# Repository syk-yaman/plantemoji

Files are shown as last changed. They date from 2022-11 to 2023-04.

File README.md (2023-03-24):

# Plantemoji: a smart IoT plant caring system

A smart plant caring and irrigation device with a web infrastructure to monitor and control plants environment and explain their living state in emojis. Basically, your plant will have AI and will be able to talk with you using emojis!

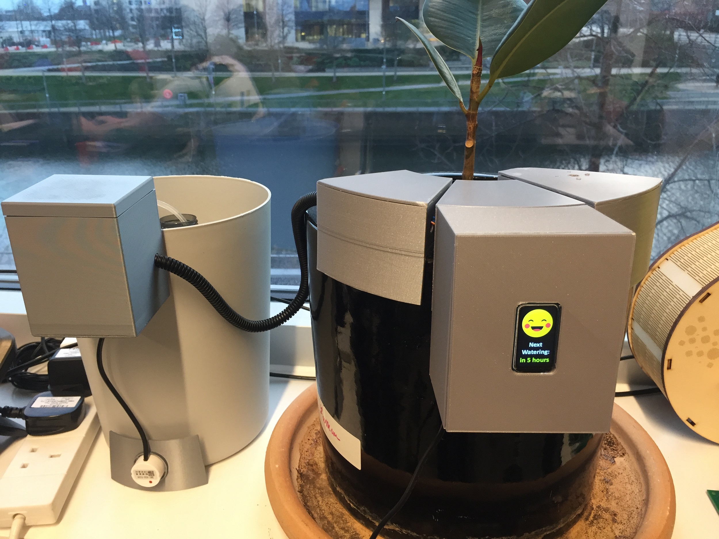
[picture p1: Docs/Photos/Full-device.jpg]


Plant container			          							 |Water bucket	 
:-----------------------------------------------------------:|:-------------------------------------------------------------------------:|
System components overview|   System components overview

## Repository Content Summary

1. **3D Enclosures**

   This section includes the 3D printed parts, namely Fusion360 project files and STLs.

   - [Plant pot](</3D Enclosures/Plant pot/>)
   - [Water bucket](</3D Enclosures/Water bucket/>)

2. **Code**

   Includes micro-controllers' code, Artificial Intelligence code and various assets used during development.

   - [AI](/Code/AI)

     [LSTM.py](/Code/AI/LSTM.py) is the main Python script where the LSTM neural network is developed and trained. This folder also contains the old [Colab experiments](/Code/AI/Colab expirements/), which are obsolete and currently kept for archiving purposes. Finally, the [Results](/Code/AI/Results/) folder, which contains experiments' charts for both the LSTM.py and the obsolete Colab experiments.

   - [Assets](/Code/Assets)

     Contains `.bmp` files to be visualised on the screen, in addition to their original Photoshop files `.psd`

   - [ATMega8A](/Code/ATMega8A)

     C program for the AVR micro-controller.

   - [ESP32](/Code/ESP32)

     C++ code for the main micro-controller, which will replace Huzzah.

   - [Huzzah](/Code/Huzzah)

     C++ code for the old micro-controller. It will replaced by ESP32.

3. **Datasets**

   Includes 1 month dataset (the [full dataset](/Datasets/Full)) and other partial datasets used to train the AI model.

   This section also contains some [data analysis](/Datasets/Analysis/Analysis.md).

4. **Docs**

   This folder holds different kinds of documentation and images produced during project life time.

5. **PCB**

   The electronic side of the project. This section contains Eagle files and CAM outputs sent to PCB manufacturers.

6. **Server**

   Docker Composer file for InfluxDB and Grafana. Basically, all data acquisition is being managed by this Docker image.

## Project Overview

This conceptual diagram explains how the system is composed, down from reading sensors and understanding their values, and later sending them up to the cloud for further analysis and visualisation.

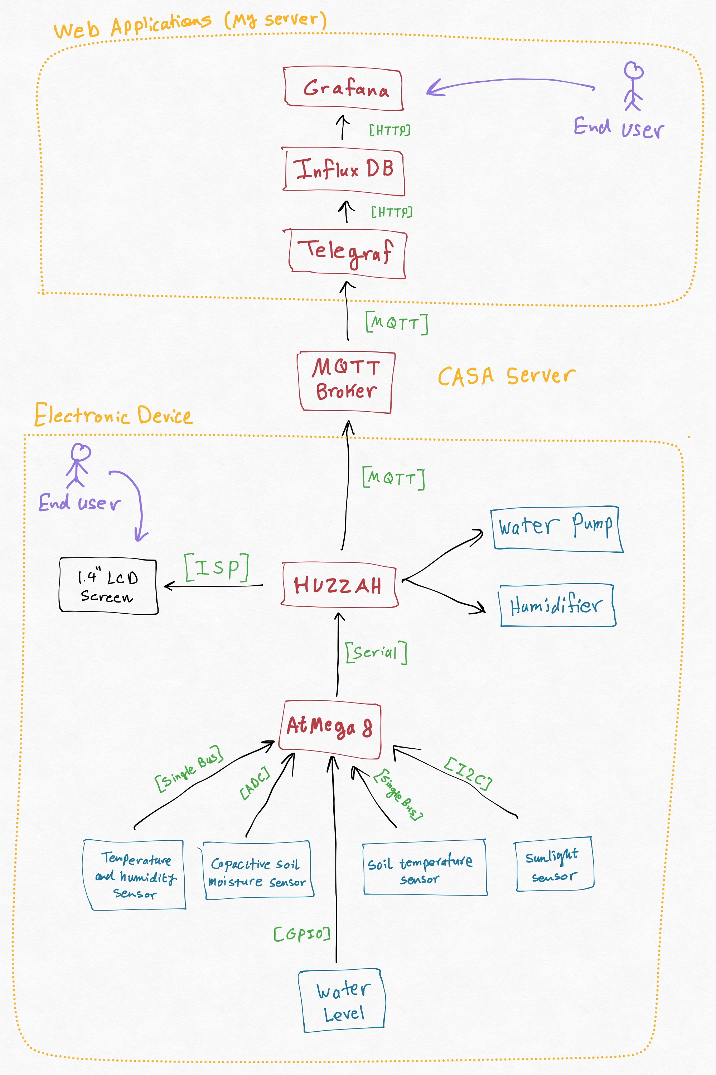
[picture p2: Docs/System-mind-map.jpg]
System components overview


The objectives of this plant monitor are:
 - Interpret sensor data for the end user in a human-friendly way.
 - Take into consideration plant living requirements during the monitoring process.
 - Make comparisons between different soil moisture sensors and the same sensor in different conditions.

## Building

### Used components and tools

Hardware:
 - [Arduino UNO](https://store.arduino.cc/products/arduino-uno-rev3)
 - [Adafruit Feather HUZZAH ESP8266](https://learn.adafruit.com/adafruit-feather-huzzah-esp8266/)
 - Huzzah-DHT22 CASA shield ([From here](https://github.com/ucl-casa-ce/casa0014/blob/main/plantMonitor/README.md#multiple-physical-prototypes))
 - [DH22](https://www.adafruit.com/product/385): Humidity and temperature sensor 
 - [HW-390](https://thepihut.com/products/capacitive-soil-moisture-sensor?variant=32137736421438): Capacitive Soil Moisture Sensor 
 - [Waveshare 1.47" LCD Dislay](https://thepihut.com/products/1-47-rounded-spi-lcd-display-module-172x320?variant=42062646509763)

Software:
 - [InfluxDB](https://www.influxdata.com/)
 - [Telegraf](https://www.influxdata.com/time-series-platform/telegraf/)
 - [Grafana](https://grafana.com/)
 - [Docker Compose](https://docs.docker.com/compose/)

All the software applications are packed into one [Docker image](/Server/docker-compose.yml) that you can use easily.

Tools:
 - [Image2Lcd](https://www.waveshare.com/wiki/File:Image2Lcd.7z): converts BMP images to byte arrays stored in MCUs to be displayed on the LCD screen (please follow [these settings](/Docs/Image2LCD%20app%20settings.jpg)).

### Hardware schematic

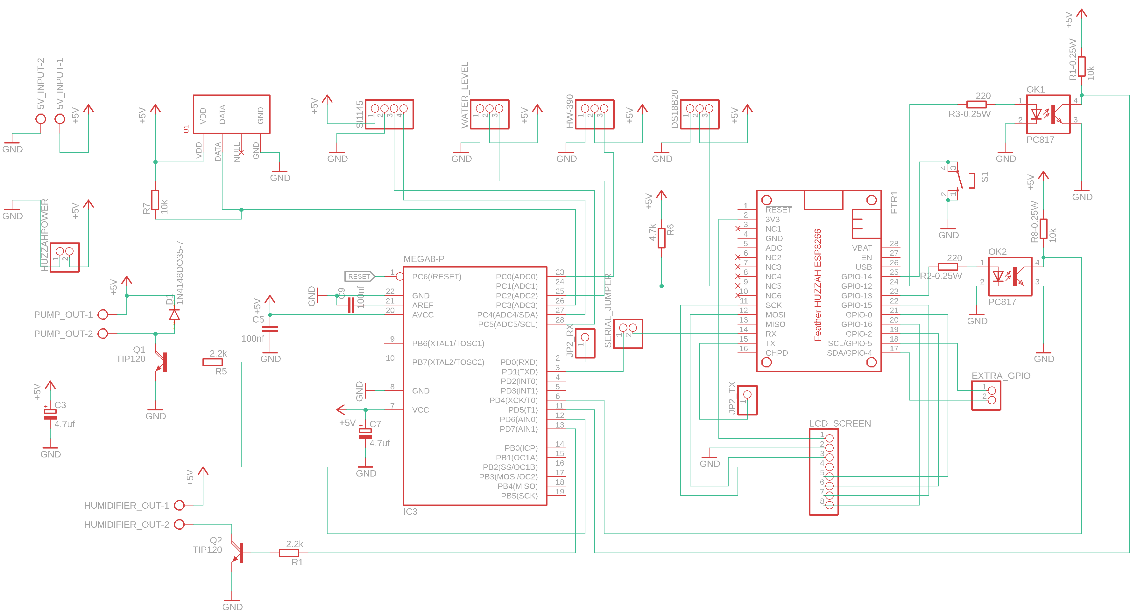
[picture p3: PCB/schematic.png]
Hardware schematic


### Highlights
 - Sensors are connected to Arduino now due to the availability of many ADC ports compared to HUZZAH.
 - The LCD screen driver was ported from Arduino to work on HUZZAH, the latter has more memory and capability to drive screens compared to Arduino.
 - New MQTT topics added: `moistureCapacitive` for the capacitive sensor and `mood` which is derived from sensor data according to plant profile.
 - [Plant profile](/Code/Huzzah/PlantProfile.h): a file containing the suitable living environment parameters for the desired plant. The mood of the plant (happy - sad) is determined based on this profile.

## Results
Grafana dashboard            |  InfluxDB dashboard		 |  MQTT feed
:---------------------------:|:-------------------------:|:-------------------------:
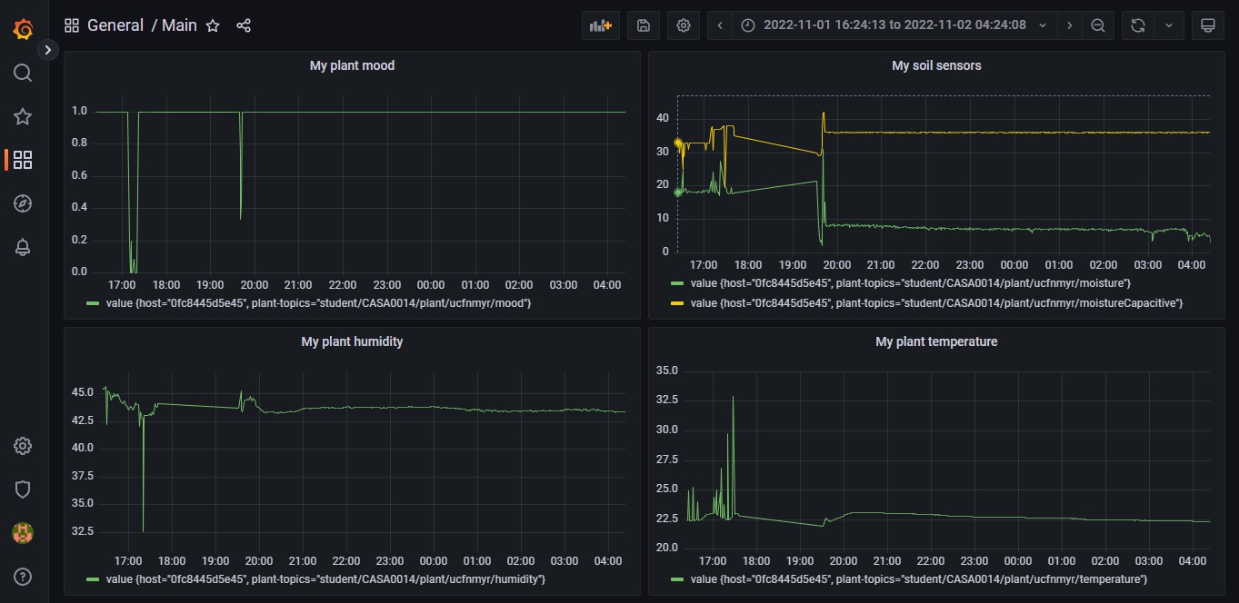
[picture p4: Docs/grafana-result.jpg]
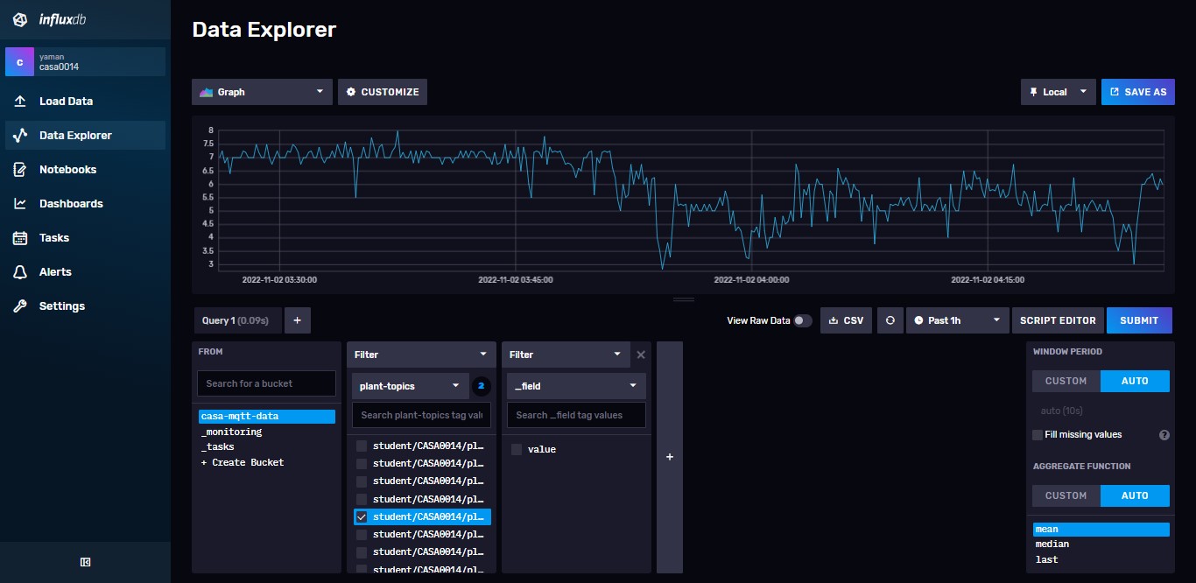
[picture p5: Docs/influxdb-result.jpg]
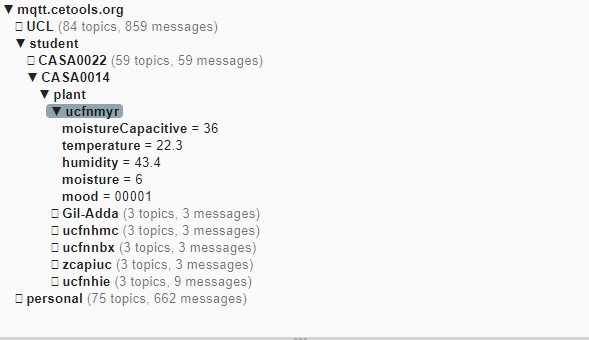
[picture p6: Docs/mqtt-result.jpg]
MQTT
|   |   

See [here](/Docs/DAQ/DAQ.md) for more detailed comparisons between sensor types.

## Future work
- Add more plants profiles.
- Let plant profile can be controlled using HTTP.
- Add mobile notifications.
- Do more comparisons with other sensor conditions.
- Add more emojis to express plant mood further.

## Resources and references
- [Capacitive sensors principles](https://makersportal.com/blog/2020/5/26/capacitive-soil-moisture-calibration-with-arduino)
- [Serial communication](https://circuitdigest.com/microcontroller-projects/arduino-spi-communication-tutorial)
- [InfluxDB course](https://university.influxdata.com/courses/influxdb-essentials-tutorial/)

## Lessons learned
 - Understanding the data from a simple sensor in the real world is not easy due to the effect of environment parameters and setup conditions.
 - Remember: Always print a 3D case and try to be gentle with screens!
 - Visualising the data can make us understand the surrounding environment in a better way.
 - If a serial connection is needed between two devices with different power sources, their GND should be connected together. And of course, they also must have the same baud rate.

## License

###### The software side is licensed under MIT License

```
MIT License

Permission is hereby granted, free of charge, to any person obtaining a copy
of this software and associated documentation files (the "Software"), to deal
in the Software without restriction, including without limitation the rights
to use, copy, modify, merge, publish, distribute, sublicense, and/or sell
copies of the Software, and to permit persons to whom the Software is
furnished to do so, subject to the following conditions:

The above copyright notice and this permission notice shall be included in all
copies or substantial portions of the Software.

THE SOFTWARE IS PROVIDED "AS IS", WITHOUT WARRANTY OF ANY KIND, EXPRESS OR
IMPLIED, INCLUDING BUT NOT LIMITED TO THE WARRANTIES OF MERCHANTABILITY,
FITNESS FOR A PARTICULAR PURPOSE AND NONINFRINGEMENT. IN NO EVENT SHALL THE
AUTHORS OR COPYRIGHT HOLDERS BE LIABLE FOR ANY CLAIM, DAMAGES OR OTHER
LIABILITY, WHETHER IN AN ACTION OF CONTRACT, TORT OR OTHERWISE, ARISING FROM,
OUT OF OR IN CONNECTION WITH THE SOFTWARE OR THE USE OR OTHER DEALINGS IN THE
SOFTWARE.
```

###### The hardware side is licensed under CERN License

```
This documentation describes Open Hardware and is licensed under the CERN OHL v. 1.2.

You may redistribute and modify this documentation under the terms of the CERN OHL v.1.2. (http://ohwr.org/cernohl). This documentation is distributed WITHOUT ANY EXPRESS OR IMPLIED WARRANTY, INCLUDING OF MERCHANTABILITY, SATISFACTORY QUALITY AND FITNESS FOR A PARTICULAR PURPOSE. Please see the CERN OHL v.1.2 for applicable conditions
```

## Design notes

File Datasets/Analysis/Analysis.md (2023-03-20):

## **A daily sudden decrease and increase in humidity (green).**

This pattern is more clear during weekends.

**My hypothesis:** This pattern probably happens when the AC is turned on and off.

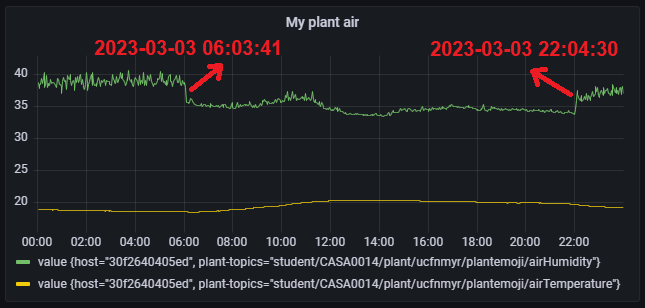
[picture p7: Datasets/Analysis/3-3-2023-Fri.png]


Figure 1: Air humidity and temperature readings on Friday, 3-3-2023

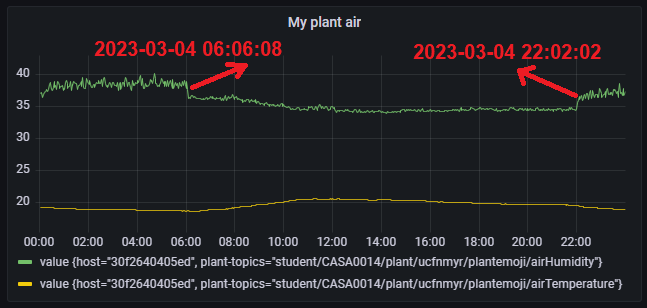
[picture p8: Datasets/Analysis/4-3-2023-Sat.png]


Figure 2: Air humidity and temperature readings on Saturday, 4-3-2023

## A sudden increase in humidity after sunlight exposure

This pattern happens sometimes after the sun has affected the environment by rising the temperature and lowering humidity. Of course, I ensured that the yellow line (temperature) corresponded with sunlight from my UV readings. 

**My hypothesis:** Could the AC be reacting to the sudden increase in temperature by working in cooling mode? 

If this is not the case, my other hypothesis could be related to false readings from the DHT22 I'm using, it may need recalibration after being affected by direct sunlight.

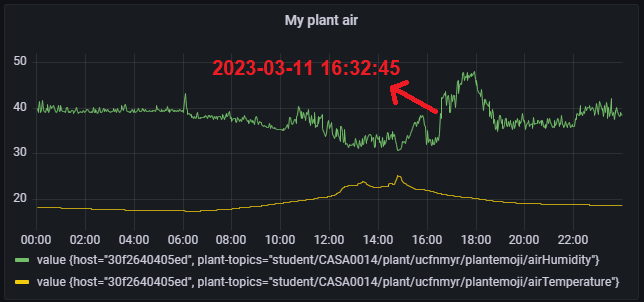
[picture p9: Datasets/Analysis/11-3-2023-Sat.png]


Figure 3: Air humidity and temperature readings on Saturday, 11-3-2023

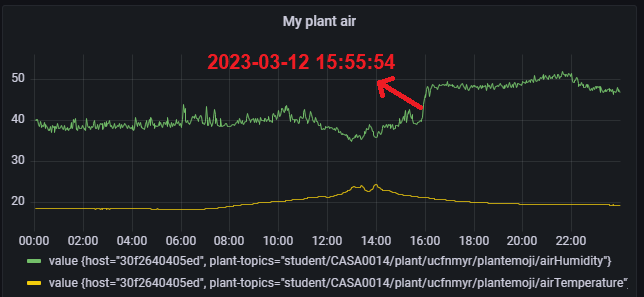
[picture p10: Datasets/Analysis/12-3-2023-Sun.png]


Figure 4: Air humidity and temperature readings on Sunday, 12-3-2023

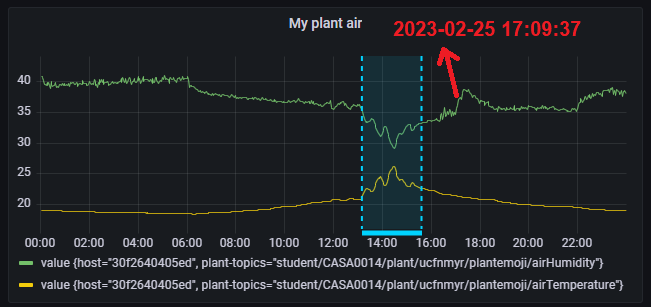
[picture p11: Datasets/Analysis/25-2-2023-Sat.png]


Figure 5: Air humidity and temperature readings on Saturday, 25-2-2023

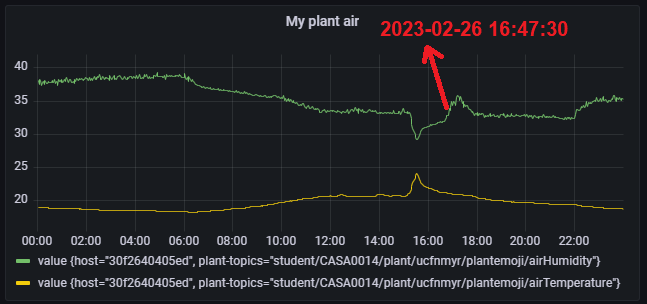
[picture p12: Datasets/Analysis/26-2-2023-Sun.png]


Figure 6: Air humidity and temperature readings on Sunday, 26-2-2023

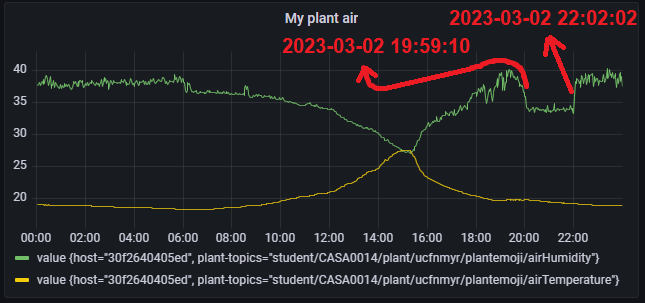
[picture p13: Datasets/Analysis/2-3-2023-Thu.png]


Figure 7: Air humidity and temperature readings on Thursday, 2-3-2023. **Note:** The right timestamp is probably related to the AC being turned off.

## Discussion with Will about the previous results

These are good graphs and seem to show a useful pattern and give insight to the AC operation as you say. It can’t hurt to recalibrate the sensor, so go ahead with that if you’re worried about errors. Generally, though, I think that you have a good insight of what is going on. One think that I would be wary of though is that you mention your sensors are exposed to direct sunlight. Normally you would put temperature sensors away from windows where they might be affected by direct sunlight to assess room conditions. As your sensor is meant for plant health monitoring, if your plant is in the sun, it might make sense to measure the temperature there, but now that you are using it to make assessments of building systems, I would avoid placing sensors in locations where they could be exposed to direct sunlight where possible.

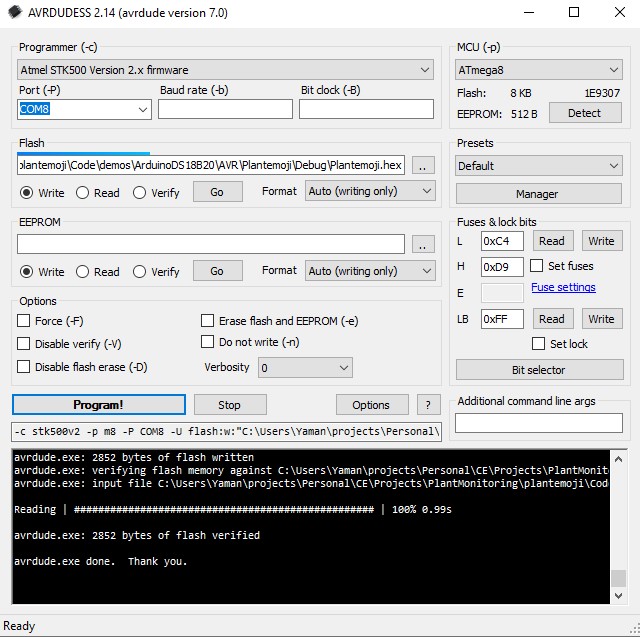
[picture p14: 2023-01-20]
Docs/ATMega8A flash settings.jpg

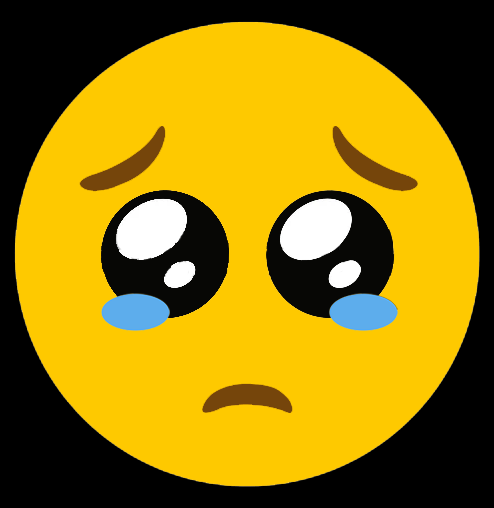
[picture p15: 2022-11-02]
Code/Assets/sad-face.bmp

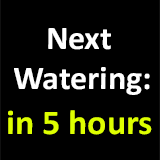
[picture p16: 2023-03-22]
Code/Assets/next-watering.bmp

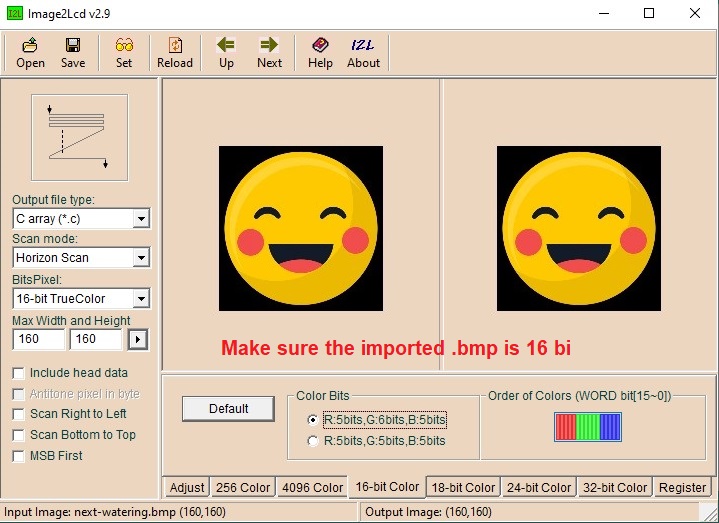
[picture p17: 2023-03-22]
Docs/Image2LCD app settings.jpg

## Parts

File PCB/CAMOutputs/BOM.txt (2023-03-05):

Qty Value        Device              Package          Parts                                             Description                                                   ARROW_PART_NUMBER ARROW_PRICE-STOCK                                            DESCRIPTION                                                   HEIGHT MANUFACTURER_NAME MANUFACTURER_PART_NUMBER MF MOUSER_PART_NUMBER MOUSER_PRICE-STOCK                                                                         MPN          OC_FARNELL OC_NEWARK POPULARITY PROD_ID  
1                10-XX               B3F-10XX         S1                                                OMRON SWITCH                                                                                                                                                                                                                                                                                                                                                                  B3F-1000     176432     36M3542   72                  
3                AK500/2             AK500/2          5V_INPUT, HUMIDIFIER_OUT, PUMP_OUT                CONNECTOR                                                                                                                                                                                                                                                                                                                                                                                  unknown    unknown                       
2                PINHD-1X1           1X01             JP2_RX, JP2_TX                                    PIN HEADER                                                                                                                                                                                                                                                                                                                                                                                                      64                  
5                PINHD-1X2           1X02             B_POWER, ESP_POWER, EX_GPIO, EX_IO, SERIAL_JUMPER PIN HEADER                                                                                                                                                                                                                                                                                                                                                                                                      98                  
3                PINHD-1X3           1X03             DS18B20, HW-390, WATER_LEVEL                      PIN HEADER                                                                                                                                                                                                                                                                                                                                                                                                      92                  
1                PINHD-1X4           1X04             SI1145                                            PIN HEADER                                                                                                                                                                                                                                                                                                                                                                                                      91                  
1                PINHD-1X8           1X08             LCD_SCREEN                                        PIN HEADER                                                                                                                                                                                                                                                                                                                                                                                                      67                  
1                RHT03_DHT-22_AM2302 RHT03_DHT-22     U1                                                RHT03 / DHT-22 / AM2302                                                                                                                                                                                                                                                                                                                                                                                                    SEN-10167
2   100nf        C-EU025-025X050     C025-025X050     C5, C9                                            CAPACITOR, European symbol                                                                                                                                                                                                                                                                                                                                                                                                          
3   10k          R-EU_0207/10        0207/10          R1-0.25W, R7, R8-0.25W                            RESISTOR, European symbol                                                                                                                                                                                                                                                                                                                                                                                                           
1   1N4148DO35-7 1N4148DO35-7        DO35-7           D1                                                DIODE                                                                                                                                                                                                                                                                                                                                                                                                           58                  
2   2.2k         R-EU_0207/10        0207/10          R1, R5                                            RESISTOR, European symbol                                                                                                                                                                                                                                                                                                                                                                                                           
2   220          R-EU_0207/10        0207/10          R2-0.25W, R3-0.25W                                RESISTOR, European symbol                                                                                                                                                                                                                                                                                                                                                                                                           
1   4.7k         R-EU_0207/10        0207/10          R6                                                RESISTOR, European symbol                                                                                                                                                                                                                                                                                                                                                                                                           
2   4.7uf        CPOL-EUE2.5-5       E2,5-5           C3, C7                                            POLARIZED CAPACITOR, European symbol                                                                                                                                                                                                                                                                                                                                                                                                
1   DFR0478      DFR0478             FIREBEETLE_ESP32 ESP32-FIREBEETLE                                  Development Boards & Kits - Wireless FireBeetle ESP32 IOT MCU DFR0478           https://www.arrow.com/en/products/dfr0478/dfrobot?region=nac Development Boards & Kits - Wireless FireBeetle ESP32 IOT MCU mm     DFRobot           DFR0478                     426-DFR0478        https://www.mouser.co.uk/ProductDetail/DFRobot/DFR0478?qs=EU6FO9ffTwc%252BR65h2NUGQw%3D%3D                                                       
1   MEGA8-P      MEGA8-P             DIL28-3          IC3                                               MICROCONTROLLER                                                                                                                                                                                                                                                                                                                                                                            unknown    unknown                       
2   PC817        PC817               DIL04            OK1, OK2                                          SHARP OPTO COUPLER                                                                                                                                                                                                                                                                                                                                                            PC817X4J000F 9707727    97K7059                       
2   TIP120       TIP120              TO220AH          Q1, Q2                                            NPN DARLINGTON TRANSISTOR                                                                                                                                                                                                                                                                                                                                                                                       2

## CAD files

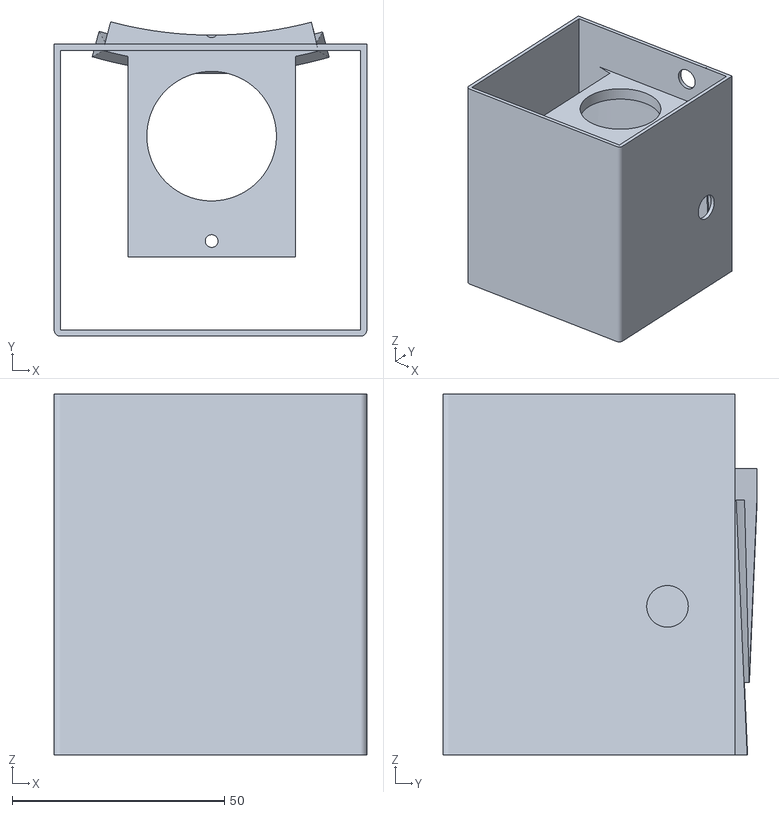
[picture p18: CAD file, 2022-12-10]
3D Enclosures/Water bucket/Water pump holder - main body.stl
73.7 x 74.0 x 85.0

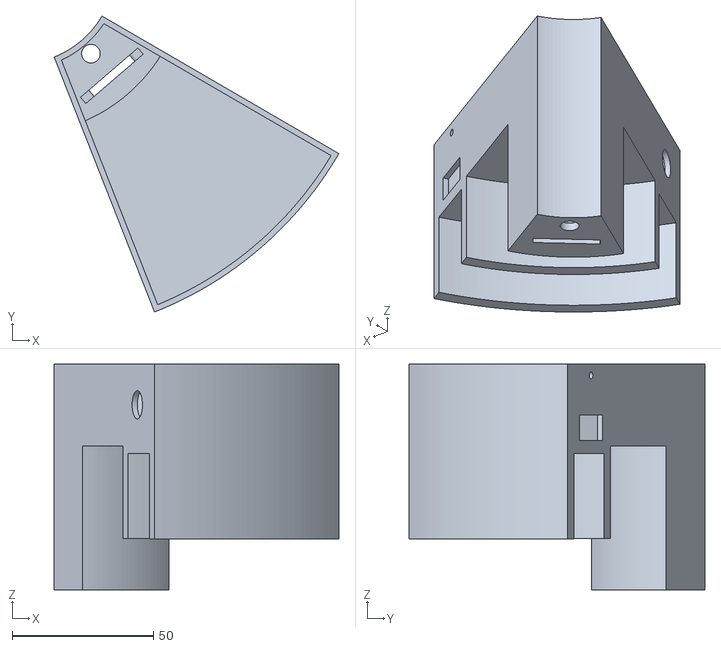
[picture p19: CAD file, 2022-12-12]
3D Enclosures/Plant pot/Sensors-body.stl
100.8 x 104.8 x 80.0

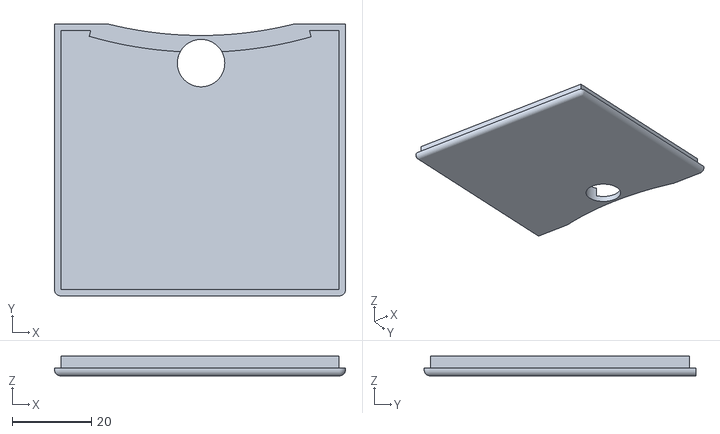
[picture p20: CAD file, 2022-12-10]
3D Enclosures/Water bucket/Water pump holder - bottom cover.stl
73.7 x 68.8 x 5.00

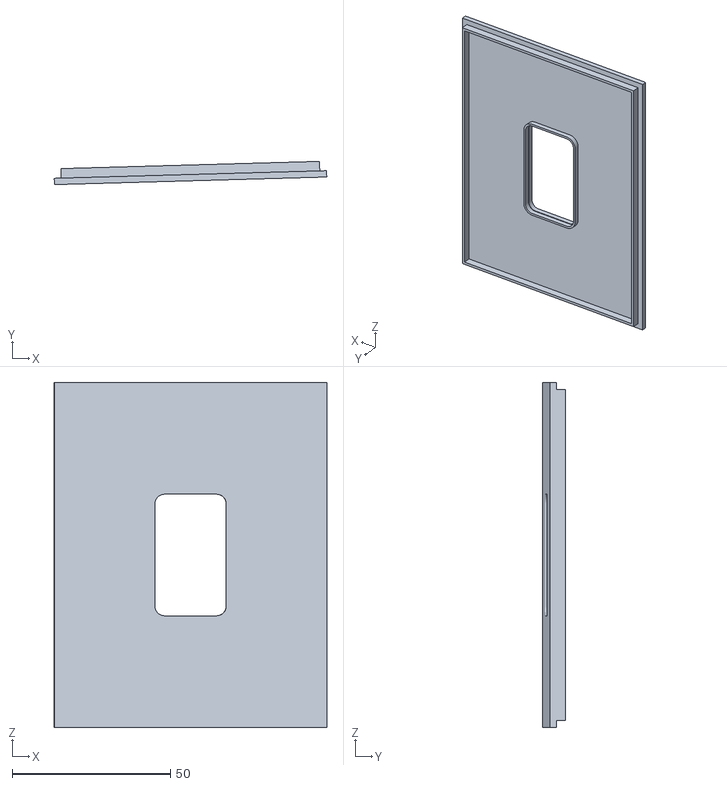
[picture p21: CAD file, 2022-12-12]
3D Enclosures/Plant pot/Screen-box-cover.stl
86.1 x 7.34 x 109.0

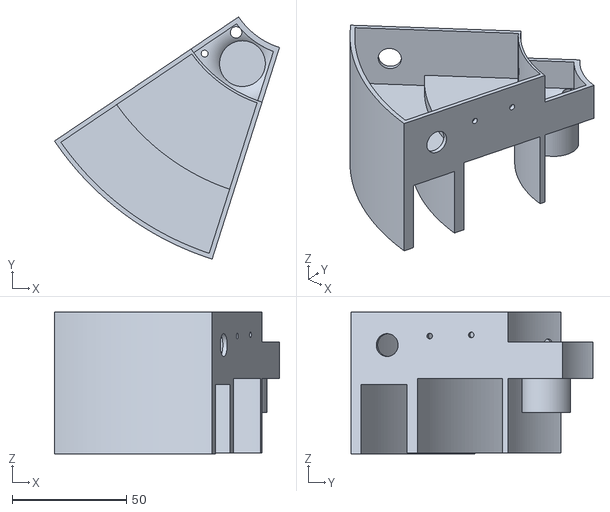
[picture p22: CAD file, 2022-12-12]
3D Enclosures/Plant pot/Water-body.stl
98.3 x 105.9 x 62.0

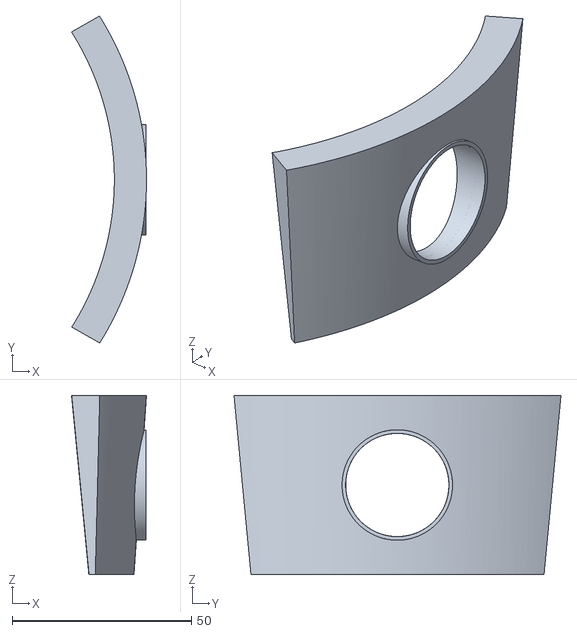
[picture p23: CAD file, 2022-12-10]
3D Enclosures/Water bucket/Water level sensor holder.stl
21.0 x 91.3 x 50.0

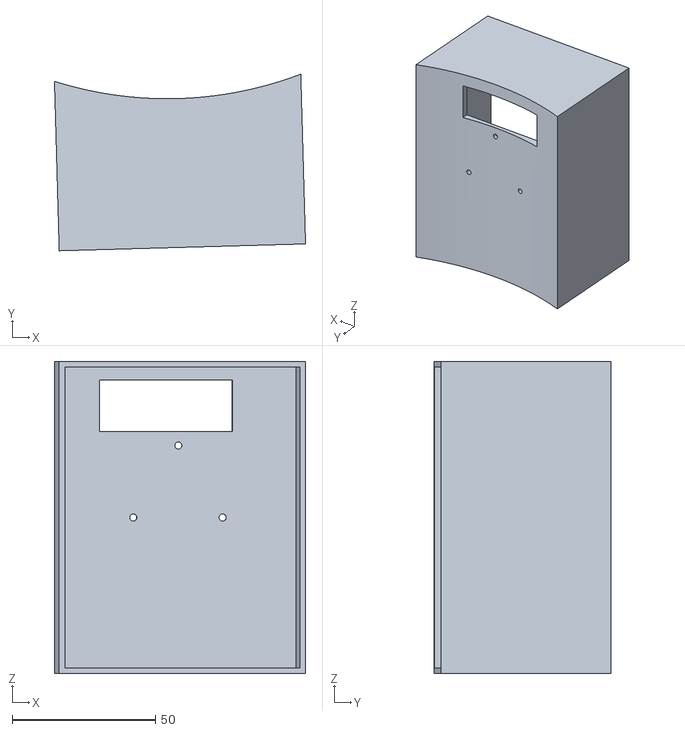
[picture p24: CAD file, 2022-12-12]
3D Enclosures/Plant pot/Screen-box.stl
87.7 x 61.7 x 109.0

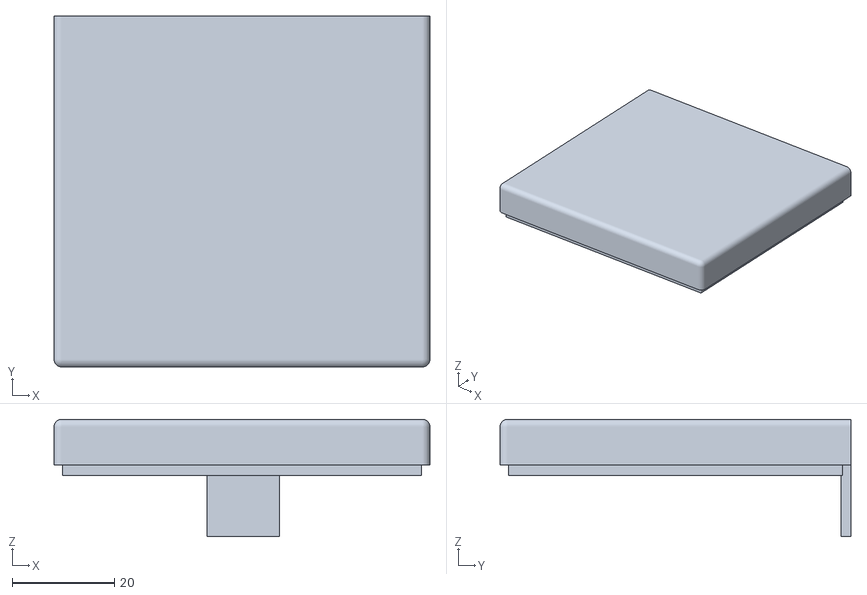
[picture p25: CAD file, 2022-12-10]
3D Enclosures/Water bucket/Water pump holder - top cover.stl
73.7 x 68.8 x 23.0

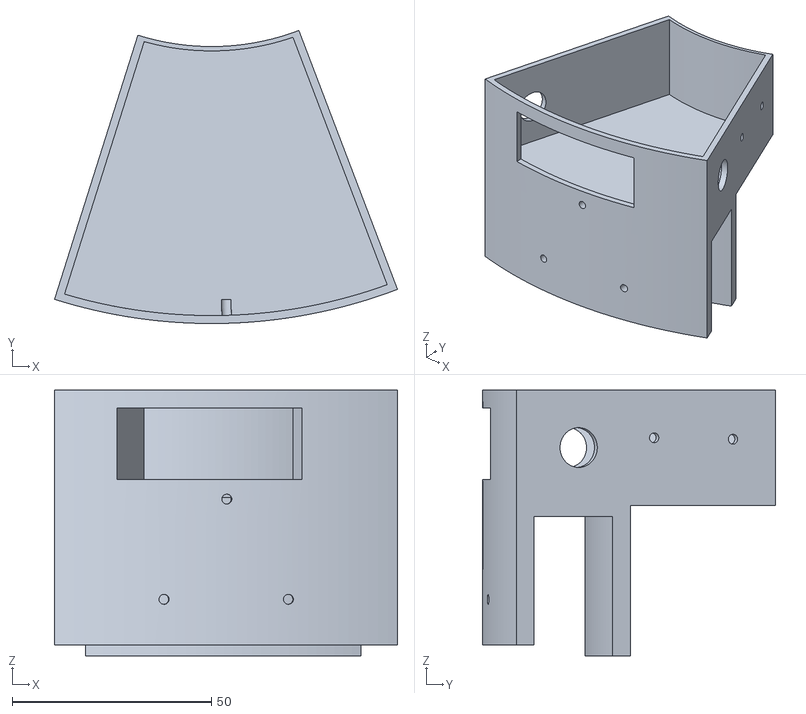
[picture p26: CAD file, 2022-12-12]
3D Enclosures/Plant pot/Screen-body.stl
86.1 x 73.5 x 66.7

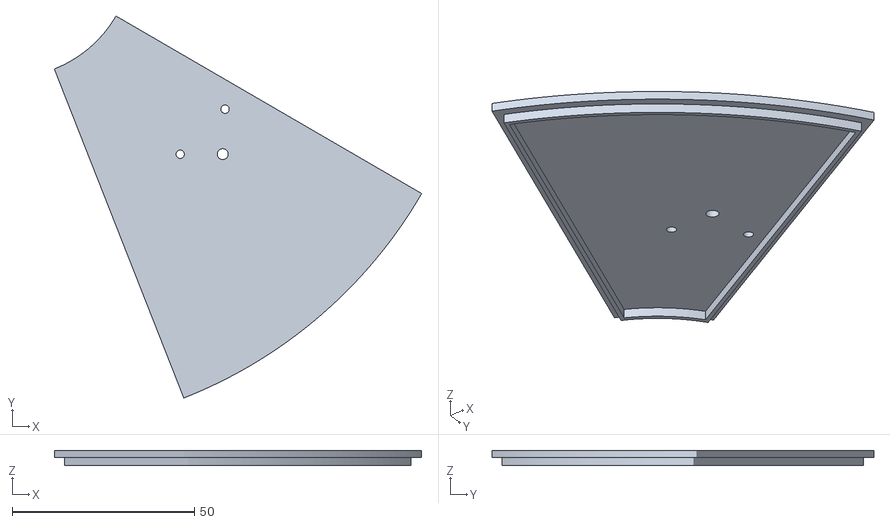
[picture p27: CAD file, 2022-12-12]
3D Enclosures/Plant pot/Sensors-cover.stl
100.8 x 104.8 x 4.20

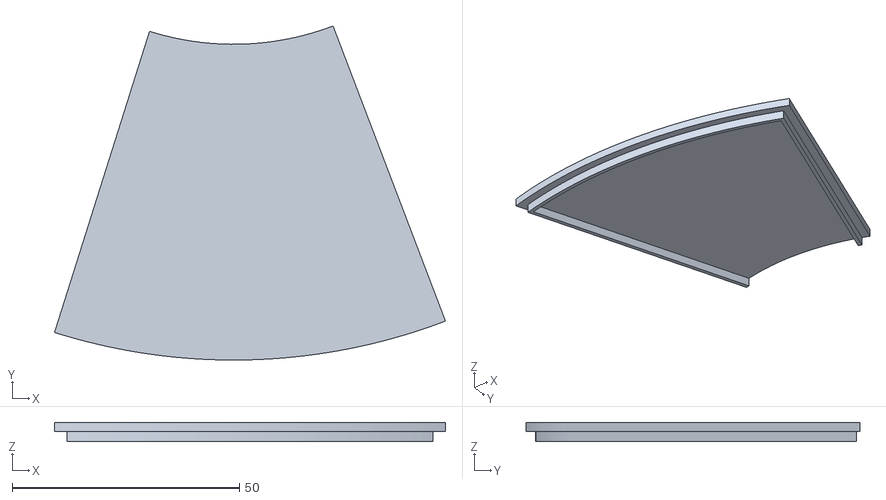
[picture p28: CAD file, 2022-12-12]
3D Enclosures/Plant pot/Screen-body-cover.stl
86.1 x 73.5 x 4.20

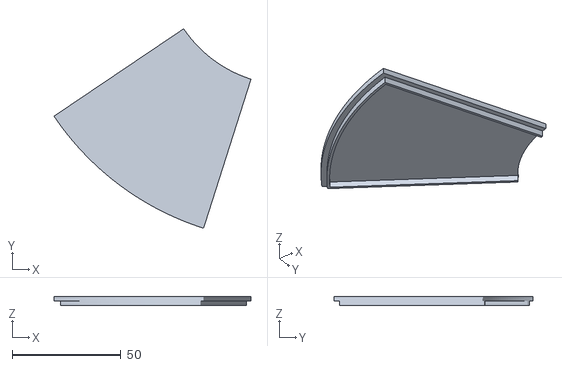
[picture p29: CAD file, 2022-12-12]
3D Enclosures/Plant pot/Water-cover.stl
90.8 x 91.9 x 4.20

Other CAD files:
3D Enclosures/Plant pot/Plant pot devices v34.f3d
3D Enclosures/Water bucket/Water bucket v15.f3d

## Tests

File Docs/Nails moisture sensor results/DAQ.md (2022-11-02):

# Soil moisture sensors comparisons

## Nail sensor with different angles between the nails

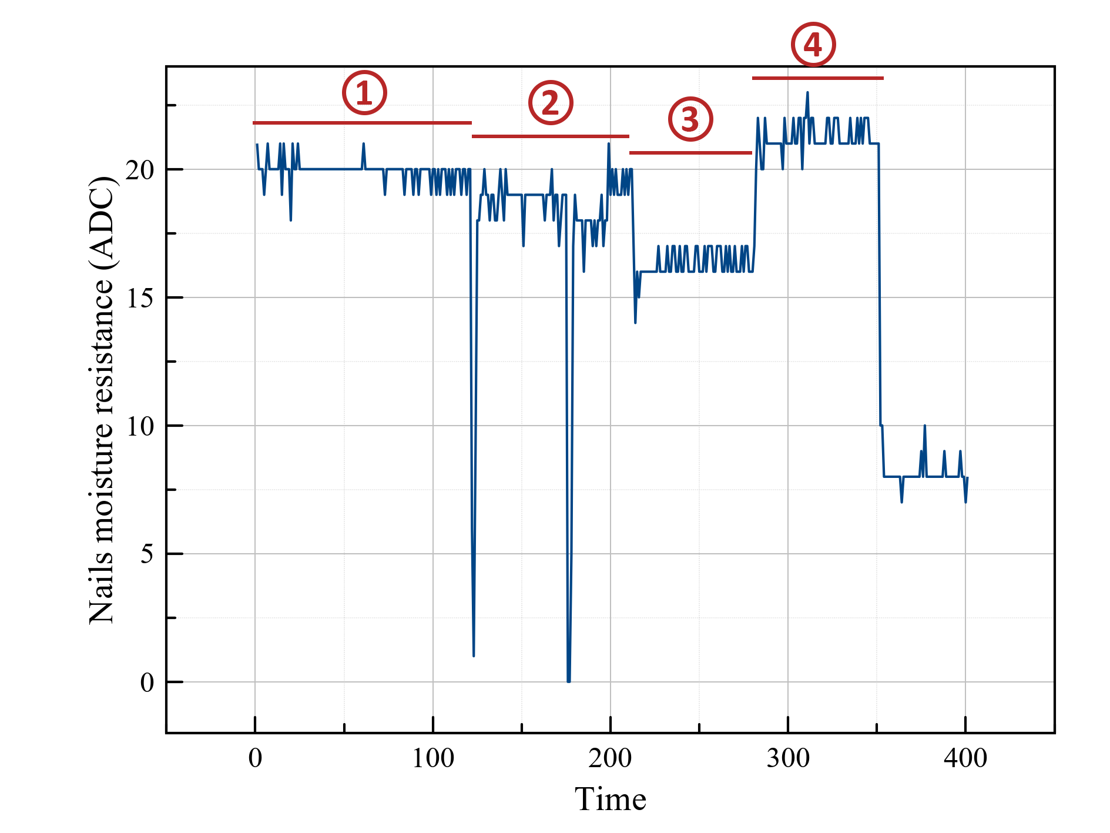
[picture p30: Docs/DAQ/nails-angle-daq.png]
Nail angle DAQ


Number indication:
1. nails' ends are closest together at 2cm inside the soil
2. nails' ends are at 3cm inside the soil
3. nails' ends are furthest at 5cm inside the soil
4. same as (3) with depth increasing

## Two nail sensor; one has new nails, and the other has corroded nails

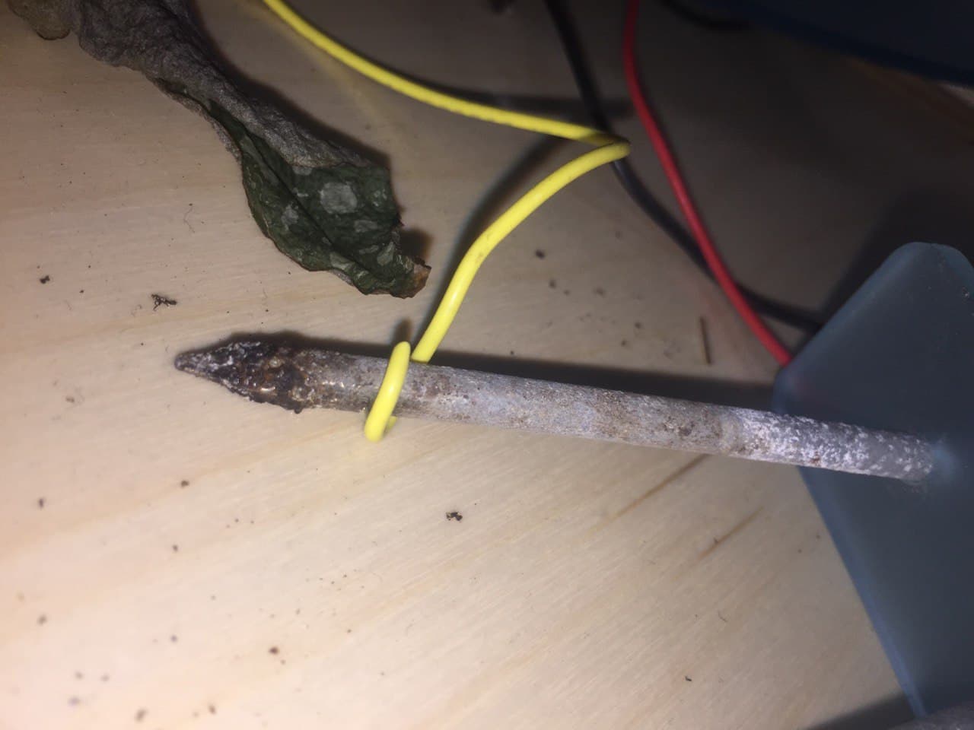
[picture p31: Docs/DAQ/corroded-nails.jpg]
Corroded nails


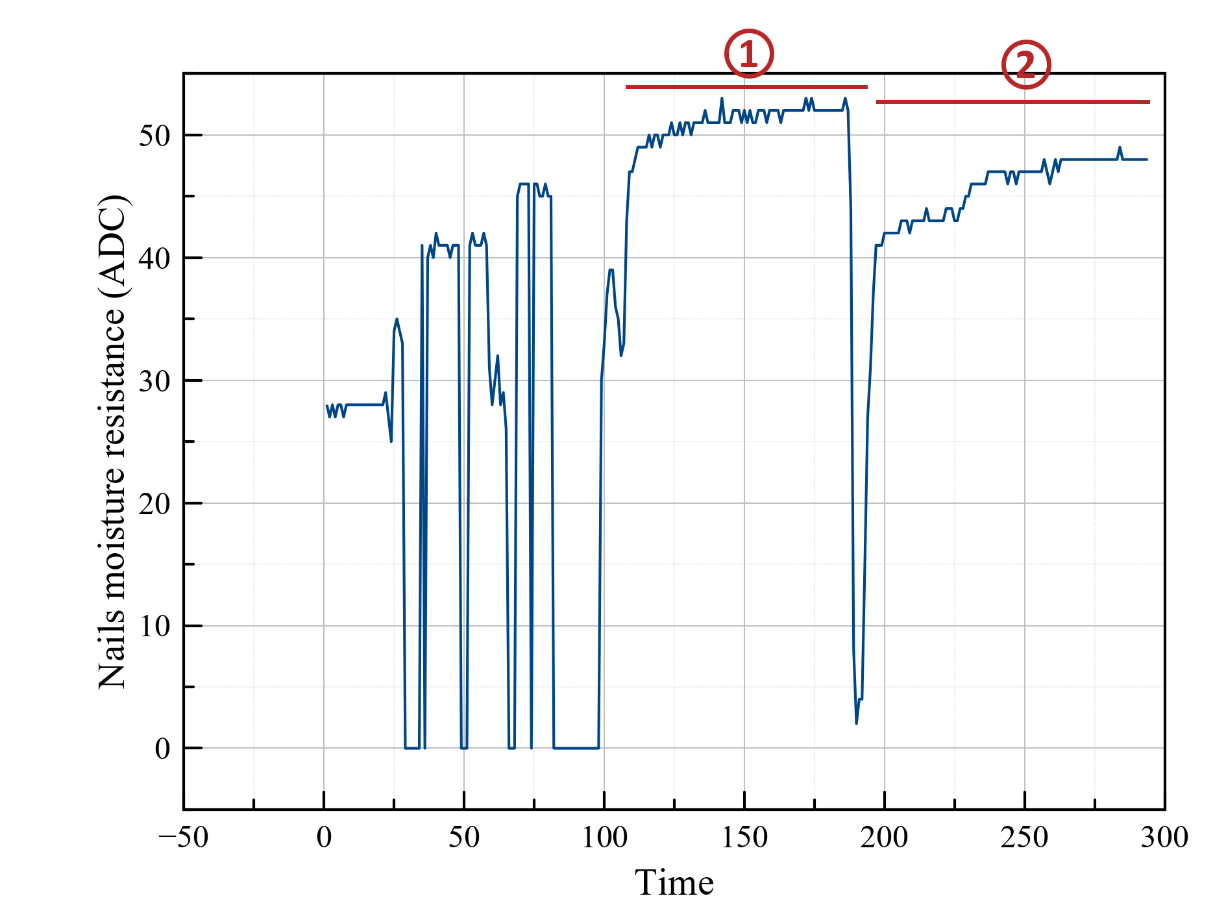
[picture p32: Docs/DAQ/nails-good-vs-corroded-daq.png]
Nail corrosion DAQ


Number indication:
1. good nails
2. corroded nails

## Capacitive sensor with different depth

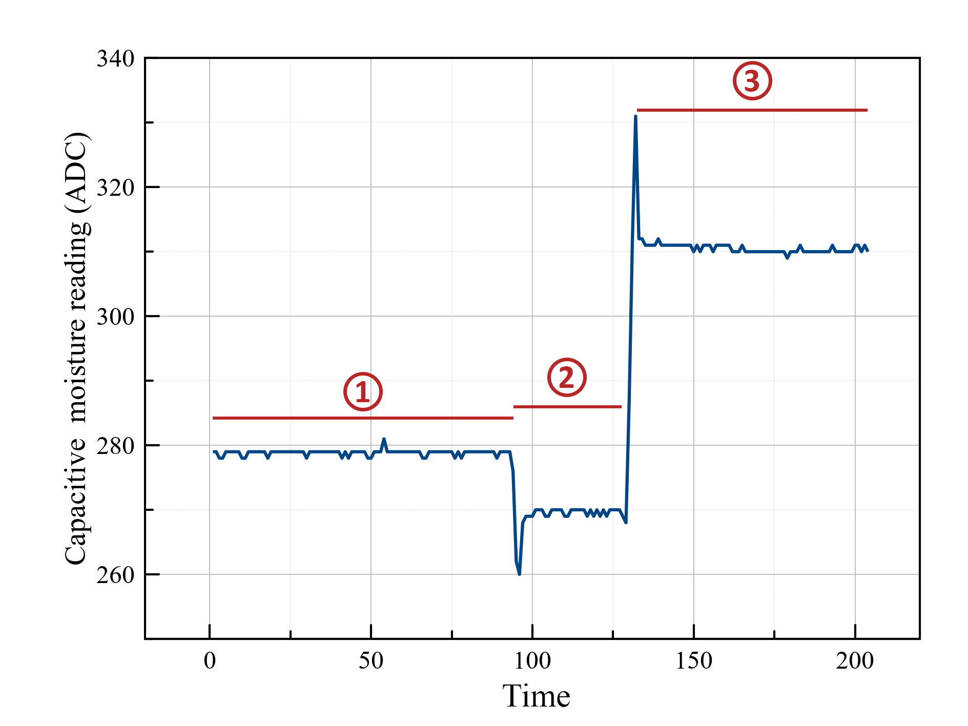
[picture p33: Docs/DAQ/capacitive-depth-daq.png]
Capacitive depth DAQ


Number indication:
1. sensor is inside the soil at the intended mark on its PCB
2. sensor is deeper inside the soil by 1cm below the mark
4. sensor is above the soil by 1cm above the mark

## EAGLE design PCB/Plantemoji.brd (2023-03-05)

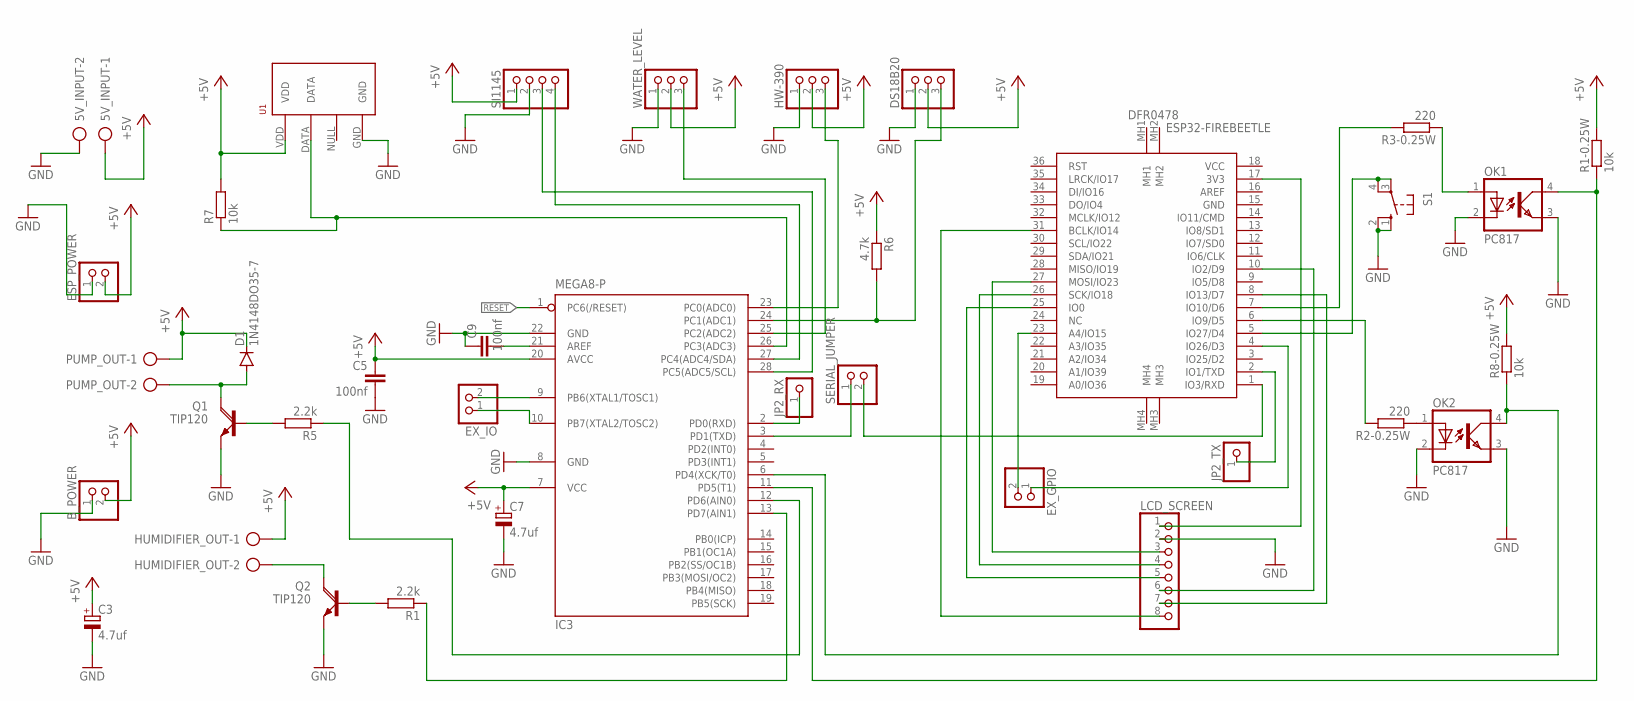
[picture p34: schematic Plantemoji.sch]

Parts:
5V_INPUT: AK500/2
B_POWER: PINHD-1X2; 1X02
C3, C7: 4.7uf; E2,5-5
C5, C9: 100nf; C025-025X050
D1: 1N4148DO35-7; DO35-7
DS18B20: PINHD-1X3; 1X03
ESP32-FIREBEETLE: DFR0478; FIREBEETLE_ESP32
ESP_POWER: PINHD-1X2; 1X02
EX_GPIO: PINHD-1X2; 1X02
EX_IO: PINHD-1X2; 1X02
HUMIDIFIER_OUT: AK500/2
HW-390: PINHD-1X3; 1X03
IC3: MEGA8-P; DIL28-3
JP2_RX, JP2_TX: PINHD-1X1; 1X01
LCD_SCREEN: PINHD-1X8; 1X08
OK1, OK2: PC817; DIL04
PUMP_OUT: AK500/2
Q1, Q2: TIP120; TO220AH
R1, R5: 2.2k; 0207/10
R1-0.25W, R7, R8-0.25W: 10k; 0207/10
R2-0.25W, R3-0.25W: 220; 0207/10
R6: 4.7k; 0207/10
S1: 10-XX; B3F-10XX
SERIAL_JUMPER: PINHD-1X2; 1X02
SI1145: PINHD-1X4; 1X04
U1: RHT03_DHT-22_AM2302; RHT03_DHT-22
WATER_LEVEL: PINHD-1X3; 1X03

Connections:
+5V: 5V_INPUT.1, B_POWER.2, C3.+, C5.1, C7.+, D1.C, DS18B20.2, ESP_POWER.2, HUMIDIFIER_OUT.1, HW-390.2, IC3.7 (VCC), IC3.20 (AVCC), PUMP_OUT.1, R1-0.25W.2, R6.1, R7.2, R8-0.25W.2, SI1145.1, U1.VDD, WATER_LEVEL.2
GND: 5V_INPUT.2, B_POWER.1, C3.-, C5.2, C7.-, C9.2, DS18B20.1, ESP_POWER.1, HW-390.1, IC3.8 (GND), IC3.22 (GND), LCD_SCREEN.2, OK1.2 (C), OK1.3 (EMIT), OK2.2 (C), OK2.3 (EMIT), Q1.E, Q2.E, S1.1 (S), S1.2 (S1), SI1145.2, U1.GND, WATER_LEVEL.1
unnamed: ESP32-FIREBEETLE.5 (IO27/D4), S1.3, S1.4 (P1)
unnamed: IC3.3 (PD1(TXD)), SERIAL_JUMPER.1
unnamed: ESP32-FIREBEETLE.1 (IO3/RXD), SERIAL_JUMPER.2
unnamed: ESP32-FIREBEETLE.17 (3V3), LCD_SCREEN.1
unnamed: ESP32-FIREBEETLE.27 (MOSI/IO23), LCD_SCREEN.3
unnamed: ESP32-FIREBEETLE.26 (SCK/IO18), LCD_SCREEN.4
unnamed: ESP32-FIREBEETLE.8 (IO13/D7), LCD_SCREEN.7
unnamed: ESP32-FIREBEETLE.25 (IO0), LCD_SCREEN.5
unnamed: ESP32-FIREBEETLE.10 (IO2/D9), LCD_SCREEN.6
unnamed: IC3.6 (PD4(XCK/T0)), OK2.4 (COL), R8-0.25W.1
unnamed: OK2.1 (A), R2-0.25W.1
unnamed: ESP32-FIREBEETLE.6 (IO9/D5), R2-0.25W.2
unnamed: C9.1, IC3.21 (AREF)
unnamed: OK1.1 (A), R3-0.25W.1
unnamed: ESP32-FIREBEETLE.7 (IO10/D6), R3-0.25W.2
unnamed: IC3.2 (PD0(RXD)), JP2_RX.1
unnamed: ESP32-FIREBEETLE.2 (IO1/TXD), JP2_TX.1
unnamed: D1.A, PUMP_OUT.2, Q1.C
unnamed: Q1.B, R5.2
unnamed: IC3.12 (PD6(AIN0)), R5.1
unnamed: HUMIDIFIER_OUT.2, Q2.C
unnamed: Q2.B, R1.2
unnamed: IC3.13 (PD7(AIN1)), R1.1
unnamed: HW-390.3, IC3.23 (PC0(ADC0))
unnamed: IC3.25 (PC2(ADC2)), WATER_LEVEL.3
unnamed: DS18B20.3, IC3.24 (PC1(ADC1)), R6.2
unnamed: IC3.26 (PC3(ADC3)), R7.1, U1.DATA
unnamed: IC3.28 (PC5(ADC5/SCL)), SI1145.3
unnamed: IC3.27 (PC4(ADC4/SDA)), SI1145.4
unnamed: ESP32-FIREBEETLE.31 (BCLK/IO14), LCD_SCREEN.8
unnamed: ESP32-FIREBEETLE.23 (A4/IO15), EX_GPIO.2
unnamed: EX_IO.2, IC3.9 (PB6(XTAL1/TOSC1))
unnamed: EX_IO.1, IC3.10 (PB7(XTAL2/TOSC2))
unnamed: ESP32-FIREBEETLE.4 (IO26/D3), EX_GPIO.1
unnamed: IC3.11 (PD5(T1)), OK1.4 (COL), R1-0.25W.1
RESET: IC3.1 (PC6(/RESET))

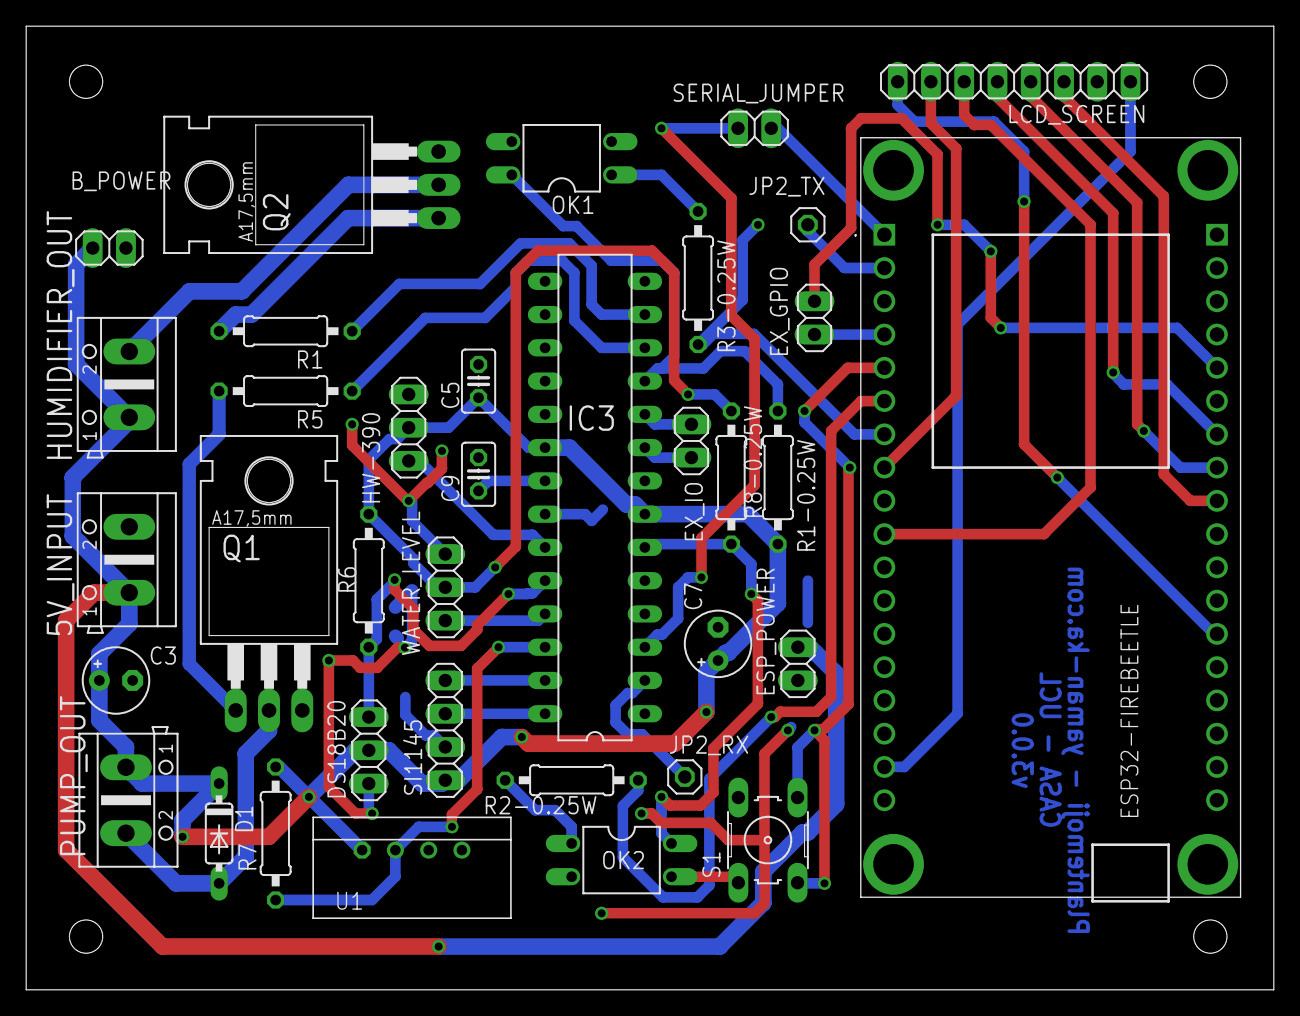
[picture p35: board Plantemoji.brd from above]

Board: 2 copper layers, 95.3 x 73.6 mm, 36 parts (0 on the bottom side), 37 nets.

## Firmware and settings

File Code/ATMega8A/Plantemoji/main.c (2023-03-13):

#include <avr/io.h>
#include <util/delay.h>
#include <stddef.h>
#include "ds18b20/ds18b20.h"
#include "dht22/DHT.h"
#include "si1145/SI1145_WE.h"

//Macros
#define bit_is_low(sfr,bit)(!(_SFR_BYTE(sfr) & _BV(bit)))
#define bit_is_high(sfr,bit)(_SFR_BYTE(sfr) & _BV(bit))
#define PORT_ON(port,pin) port |= (1<<pin)
#define PORT_OFF(port,pin)  port &= ~(1<<pin)

//Head of methods
void USART_Init( unsigned int ubrr);
void USART_Transmit( unsigned char data );
void usart_putchar( char data );
void usart_pstr (char *s);
void initPorts();
void handleSi1145Failure(unsigned char code);
int ADCsingleREAD(uint8_t adctouse);
void pumpControl(int isOn);
void humidifierControl(int isOn);

#define BAUD 115200
#define BAUDRATE F_CPU/16/BAUD-1
const float V_REF = 5.0; //reference voltage for the ADC

#define FOSC 8000000// Clock Speed
#define MYUBRR FOSC/16/BAUD-1

//global states
int pumpStatus = 0;
int humidifierStatus = 0;

//Version 1.2.0
int main()
{
	/************************************************************************/
	/* UART and ADC Initialisation										    */
	/************************************************************************/
	initPorts();
	OSCCAL=0x93;
	USART_Init(MYUBRR);
	
	ADCSRA |= (1<<ADEN); //enable ADC
	ADMUX |= ( (0<<REFS1) | (1<<REFS0) ); // set to ref to AVCC & AREF with capacitor
	ADMUX |= 5;
	
	/************************************************************************/
	/* DHT Initialisation                                                   */
	/************************************************************************/
	double airTemperature_dht22[1];
	double airHumidity_dht22[1];
	DHT_Setup();
	
	/************************************************************************/
	/* Si1145 Initialisation                                                */
	/************************************************************************/
	SI1145_WE_init(0x60);
	
	enableHighSignalVisRange(); // Gain divided by 14.5
	enableHighSignalIrRange(); // Gain divided by 14.5
	
	enableMeasurements(PSALSUV_TYPE, AUTO); /* choices: PS_TYPE, ALS_TYPE, PSALS_TYPE, ALSUV_TYPE, PSALSUV_TYPE || FORCE, AUTO, PAUSE */
	
	
	while(1)
	{
		
		/*****************************************************************************/
		/* Checking and acting upon pump & humidifier control signal from Huzzah     */
		/*****************************************************************************/
		
		if(bit_is_low(PIND,4)){
			pumpControl(1);
		} else {
			pumpControl(0);
		}
		
		if(bit_is_low(PIND,5)){
			humidifierControl(1);
			} else {
			humidifierControl(0);
		}
		
		/************************************************************************/
		/* DS18B20 Reading                                                      */
		/************************************************************************/
		
		//Start conversion (without ROM matching) 1 << (0) means pin.0, 1 << (5) means pin.5
		ds18b20convert( &PORTC, &DDRC, &PINC, ( 1 << 1 ), NULL );

		//Delay (sensor needs time to perform conversion)
		_delay_ms(1000);

		int digitalTemperature;
		double soilTemperature_ds18b20;
		//Read temperature (without ROM matching)
		ds18b20read( &PORTC, &DDRC, &PINC, ( 1 << 1 ), NULL, &digitalTemperature);
		soilTemperature_ds18b20 = digitalTemperature/16.0; //divided by 16 according to the used library's specs
		_delay_ms(2000);
		
		/************************************************************************/
		/* DHT22 Reading                                                        */
		/************************************************************************/
		
		//Read from sensor
		enum DHT_Status_t dhtStatus = DHT_Read(airTemperature_dht22, airHumidity_dht22);
		
		//Check status
		switch (dhtStatus)
		{
			case (DHT_Ok):
			//Do something
			break;
			case (DHT_Error_Checksum):
			//Do something
			break;
			case (DHT_Error_Timeout):
			//Do something else
			break;
		}
		
		//Sensor needs 1-2s to stabilize its readings
		_delay_ms(2000);
		
		/************************************************************************/
		/* HW-390 Reading                                                       */
		/************************************************************************/
		unsigned int soilHumidityDigital = ADCsingleREAD(0);
		double soilHumidity_HW390 = 100 - soilHumidityDigital/10.24;
				
		_delay_ms(2000);
		
		/************************************************************************/
		/* Si1145 Reading                                                       */
		/************************************************************************/
		unsigned char failureCode = 0;
		unsigned int amb_als = 0;
		unsigned int amb_ir = 0;
		float uv = 0.0;
		
		amb_als = getAlsVisData();
		amb_ir = getAlsIrData();
		uv = getUvIndex();
		
		failureCode = getFailureMode();  // reads the response register
		if((failureCode&128)){  // if bit 7 is set in response register, there is a failure
			handleSi1145Failure(failureCode);
		}
		
		_delay_ms(2000);

		/************************************************************************/
		/* Combine sensor values then send them over serial to Huzzah			*/
		/************************************************************************/
		
		/************************************************************************/
		/*                                                                      */
		/*					Sensor values sent to Huzzah:                       */
		/*                                                                      */
		/*					1. Dht22: air temperature => Celsius                */
		/*					2. Dht22: air humidity => Percentage                */
		/*					3. DS18b20: soil temperature => Celsius             */
		/*					4. HW390: soil humidity  => Percentage              */
		/*					5. Si1145: light => Lux                             */
		/*					6. Si1145: infrared => Lux                          */
		/*					7. Si1145: UV => UV Index (1 to 11+)				*/
		/*					8. Pump status: (0/on  1/off) => Integer            */
		/*					9. Humidifier status: (0/on  1/off) => Integer		*/
		/*                                                                      */
		/************************************************************************/
		
		char strbuf[400];
		sprintf (strbuf, "%f,%f,%f,%f,%d,%d,%f,%d,%d\r\n",
		airTemperature_dht22[0], 
		airHumidity_dht22[0],
		soilTemperature_ds18b20, 
		soilHumidity_HW390,
		amb_als,
		amb_ir,
		uv,
		pumpStatus,
		humidifierStatus);
		usart_pstr(strbuf);

	}
	return (0);
}

void pumpControl(int isOn){
	if(isOn == 1){
		PORTD |= (1 << PIND6); //Turn on the pump
		pumpStatus = 1;
	}
	if(isOn == 0){
		PORTD &= ~(1 << PIND6);	//Turn off the pump
		pumpStatus = 0;
	}
}

void humidifierControl(int isOn){
	if(isOn == 1){
		PORTD |= (1 << PIND7); //Turn on the humidifier
		humidifierStatus = 1;
	}
	if(isOn == 0){
		PORTD &= ~(1 << PIND7);	//Turn off the humidifier
		humidifierStatus = 0;
	}
}

int ADCsingleREAD(uint8_t adctouse)
{
	int ADCval;

	ADMUX = adctouse;         // use #1 ADC
	ADMUX |= ( (0<<REFS1) | (1<<REFS0) );    // use AVcc as the reference
	ADMUX &= ~(1 << ADLAR);   // clear for 10 bit resolution
	
	ADCSRA |= (1 << ADPS2) | (1 << ADPS1) | (1 << ADPS0);    // 128 prescale for 8Mhz
	ADCSRA |= (1 << ADEN);    // Enable the ADC

	ADCSRA |= (1 << ADSC);    // Start the ADC conversion

	while(ADCSRA & (1 << ADSC));      // Thanks T, this line waits for the ADC to finish


	ADCval = ADCL;
	ADCval = (ADCH << 8) + ADCval;    // ADCH is read so ADC can be updated again

	return ADCval;
}

void handleSi1145Failure(unsigned char code){
	//char msg[400];
	switch(code){
		case SI1145_RESP_INVALID_SETTING:
		//sprintf (msg, "Invalid Setting %d \r\n", 0);
		break;
		case SI1145_RESP_PS1_ADC_OVERFLOW:
		//sprintf (msg, "PS ADC Overflow %d \r\n", 0);
		break;
		case SI1145_RESP_ALS_VIS_ADC_OVERFLOW:
		//sprintf (msg, "ALS VIS ADC Overflow %d \r\n", 0);
		break;
		case SI1145_RESP_ALS_IR_ADC_OVERFLOW:
		//sprintf (msg, "ALS IR Overflow %d \r\n", 0);
		break;
		case SI1145_RESP_AUX_ADC_OVERFLOW:
		//sprintf (msg, "AUX ADC Overflow %d \r\n", 0);
		break;
		default:
		//sprintf (msg, "Unknown Failure %d \r\n", 0);
		break;
	}
	//usart_pstr(msg); //disable printing errors for now
	
	clearFailure();
}

void initPorts(){
	DDRB = 0x00; // Set PORT B to input
	DDRD |= (1 << DDB6); // Set Pin D6 (pump transistor control) as output
	DDRD |= (1 << DDB7); // Set Pin D7 (humidifier transistor control) as output
	 
	DDRD &= ~(1 << PIND4); // Set Pin D4 (pump control signal from Huzzah) as input
	DDRD &= ~(1 << PIND5); // Set Pin D5 (humidifier control signal from Huzzah) as input
	
	PORTD &= ~(1 << PIND6); //off by default
	PORTD &= ~(1 << PIND7); //off by default
}


void USART_Init( unsigned int ubrr)
{
	/* Set baud rate */
	UBRRH = (unsigned char)(ubrr>>8);
	UBRRL = (unsigned char)ubrr;
	/* Enable receiver and transmitter */
	UCSRB = (1<<RXEN)|(1<<TXEN);
	// Enable the receiver interrupt
	UCSRB |= (1 << RXCIE);
	/* Set frame format: 8data, 2stop bit */
	//UCSRC = (1<<URSEL)|(1<<USBS)|(3<<UCSZ0);
	UCSRC = (1<<URSEL)|(3<<UCSZ0);
}
void USART_Transmit( unsigned char data )
{
	/* Wait for empty transmit buffer */
	while ( !( UCSRA & (1<<UDRE)) );
	/* Put data into buffer, sends the data */
	UDR = data;
}


void usart_putchar(char data) {
	// Wait for empty transmit buffer
	while ( !(UCSRA & (_BV(UDRE))) );
	// Start transmission
	UDR = data;
}

void usart_pstr(char *s) {
	// loop through entire string
	while (*s) {
		usart_putchar(*s);
		s++;
	}
}

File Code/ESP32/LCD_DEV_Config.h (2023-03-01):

/*****************************************************************************
* | File        :   DEV_Config.c
* | Author      :   Waveshare team
* | Function    :   Hardware underlying interface
* | Info        :
*                Used to shield the underlying layers of each master 
*                and enhance portability
*----------------
* | This version:   V1.0
* | Date        :   2018-11-22
* | Info        :

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
******************************************************************************/
#ifndef _DEV_CONFIG_H_
#define _DEV_CONFIG_H_

#include <stdint.h>
#include <stdio.h>
#include <SPI.h>
#include "LCD_Debug.h"
#include <pgmspace.h>
#include <Arduino.h>
#include <analogWrite.h>

#define UBYTE   uint8_t
#define UWORD   uint16_t
#define UDOUBLE uint32_t

/**
 * GPIO config
**/
#define DEV_CS_PIN  0
#define DEV_DC_PIN  2
#define DEV_RST_PIN 13
#define DEV_BL_PIN  14


/**
 * GPIO read and write
**/
#define DEV_Digital_Write(_pin, _value) digitalWrite(_pin, _value == 0? LOW:HIGH)
#define DEV_Digital_Read(_pin) digitalRead(_pin)


/**
 * SPI
**/
#define DEV_SPI_WRITE(_dat)   SPI.transfer(_dat)

/**
 * delay x ms
**/
#define DEV_Delay_ms(__xms)    delay(__xms)

/**
 * PWM_BL
**/
 #define  DEV_Set_BL(_Pin, _Value)  analogWrite(_Pin, _Value)

/*-----------------------------------------------------------------------------*/
 void Config_Init();
#endif

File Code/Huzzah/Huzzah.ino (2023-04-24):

//LCD imports
#include <SPI.h>
#include "LCD_Driver.h"
#include "LCD_GUI_Paint.h"
#include "LCD_Images.h"

//Connectivity imports
#include <ESP8266WiFi.h>
#include <PubSubClient.h>
#include "arduino_secrets.h" // Wifi and MQTT secrets 

//TimeZone import
#include <ezTime.h>

//Constants
const char* ssid     = SECRET_SSID;
const char* password = SECRET_PASS;
const char* mqttuser = SECRET_MQTTUSER;
const char* mqttpass = SECRET_MQTTPASS;   
const char* mqtt_server = "mqtt.cetools.org";

//Plant profile
#include "PlantProfile.h"

//Internal fields
WiFiClient espClient;
PubSubClient client(espClient);

int currentMood = -1;
int pumpPin = 13;
int humidifierPin = 12;

int pumpToBeOn = -1;
int humidfierToBeOn = -1;

Timezone GB;

void setup() {
  initialiseLCDScreen();
  drawMoodOnScreen(1);
  Serial.println("Hi");

  //Connect to an SSID and print local IP address, taken from CASA plant monitoring class
  Serial.print("Connecting to ");
  Serial.println(SECRET_SSID);
  WiFi.begin(SECRET_SSID, SECRET_PASS);
  while (WiFi.status() != WL_CONNECTED) {
    delay(500);
    Serial.print(".");
  }
  Serial.println("");
  Serial.println("WiFi connected");  
  Serial.println("IP address: ");
  Serial.println(WiFi.localIP());

  //Initialise time settings
  waitForSync();
  Serial.println("UTC: " + UTC.dateTime());
  GB.setLocation("Europe/London");
  Serial.println("London time: " + GB.dateTime());  

  //Initialise MQTT connection
  client.setServer(mqtt_server, 9001);
  client.setCallback(callback); 
  
  pinMode(humidifierPin, OUTPUT);
  pinMode(pumpPin, OUTPUT);
  //drawMoodOnScreen(1);
}


void loop() {
  if (!client.connected()) {
    reconnect();
  }
  client.loop();
  //When a new sensor reading is received from Arduino, it will be parsed and 
  //sent over MQTT, then the LCD screen is updated accordingly
  if (Serial.available() > 0) {
  String sensorDataReceived = "";
  sensorDataReceived = Serial.readString();
  if(sensorDataReceived != ""){
    
    /************************************************************************/
    /*                                                                      */
    /*          Sensor values order:                                        */
    /*                                                                      */
    /*          1. dht22: air temperature                                   */
    /*          2. dht22: air humidity                                      */
    /*          3. ds18b20: soil temperature                                */
    /*          4. HW390: soil humidity                                     */
    /*          5. Si1145: light                                            */
    /*          6. Si1145: infrared                                         */
    /*          7. Si1145: UV                                               */
    /*          8. Pump status: (0/on  1/off) => Integer                    */
    /*          9. Humidifier status: (0/on  1/off) => Integer              */
    /*                                                                      */
    /************************************************************************/
    
      String dht22_airTemperature = splitString(sensorDataReceived,',',0);
      String dht22_airHumidity = splitString(sensorDataReceived,',',1);
      String ds18b20_soilTemperature = splitString(sensorDataReceived,',',2);
      String hw390_soilHumidity = splitString(sensorDataReceived,',',3);
      String si1145_light = splitString(sensorDataReceived,',',4);
      String si1145_infrared = splitString(sensorDataReceived,',',5);
      String si1145_uv = splitString(sensorDataReceived,',',6);
      String pump_status = splitString(sensorDataReceived,',',7);
      String humidifier_status = splitString(sensorDataReceived,',',8);

      Serial.println("------ ATMega8A said: -------");
      Serial.println("dht22_airTemperature: " + dht22_airTemperature);
      Serial.println("dht22_airHumidity: " + dht22_airHumidity);
      Serial.println("ds18b20_soilTemperature: " + ds18b20_soilTemperature);
      Serial.println("hw390_soilHumidity: " + hw390_soilHumidity);
      Serial.println("si1145_light: " + si1145_light);
      Serial.println("si1145_infrared: " + si1145_infrared);
      Serial.println("si1145_uv: " + si1145_uv);
      Serial.println("pump_status: " + pump_status);
      Serial.println("humidifier_status: " + humidifier_status);
      
      //int mood = resolveMood(soilMoistureReading.toFloat(), humidityReading.toFloat());
      sendMQTT(
        dht22_airTemperature,
        dht22_airHumidity, 
        ds18b20_soilTemperature,  
        hw390_soilHumidity, 
        si1145_light, 
        si1145_infrared, 
        si1145_uv,
        pump_status,
        humidifier_status);
        
      //drawMoodOnScreen(mood);
    }
  
  }
}

// Decide if the plant is happy or sad according to soil moisture and humidity,
// to be developed in the future to include other sensors
int resolveMood(float soilMoistureReading, float humidityReading){
  if(soilMoistureReading > LOWER_MOISTURE_LEVEL)
  {
    return 0;
  }
  if(soilMoistureReading < LOWER_MOISTURE_LEVEL)
  {
    if(humidityReading< LOWER_HUMIDITY_LEVEL)
    {
      return 0;
    }
    return 1;
  }
}

void sendMQTT(
        String dht22_airTemperature,
        String dht22_airHumidity, 
        String ds18b20_soilTemperature,  
        String hw390_soilHumidity, 
        String si1145_light, 
        String si1145_infrared, 
        String si1145_uv,
        String pump_status,
        String humidifier_status) {

  if (!client.connected()) {
    reconnect();
  }
  client.loop();

  char msg[50];
  dht22_airTemperature.toCharArray(msg,dht22_airTemperature.length()+1);
  client.publish("student/CASA0014/plant/ucfnmyr/plantemoji/airTemperature", msg);

  dht22_airHumidity.toCharArray(msg,dht22_airHumidity.length()+1);
  client.publish("student/CASA0014/plant/ucfnmyr/plantemoji/airHumidity", msg);

  ds18b20_soilTemperature.toCharArray(msg,ds18b20_soilTemperature.length()+1);
  client.publish("student/CASA0014/plant/ucfnmyr/plantemoji/soilTemperature", msg);
  
  hw390_soilHumidity.toCharArray(msg,hw390_soilHumidity.length()+1);
  client.publish("student/CASA0014/plant/ucfnmyr/plantemoji/soilHumidity", msg);

  si1145_light.toCharArray(msg,si1145_light.length()+1);
  client.publish("student/CASA0014/plant/ucfnmyr/plantemoji/light", msg);

  si1145_infrared.toCharArray(msg,si1145_infrared.length()+1);
  client.publish("student/CASA0014/plant/ucfnmyr/plantemoji/infrared", msg);

  si1145_uv.toCharArray(msg,si1145_uv.length()+1);
  client.publish("student/CASA0014/plant/ucfnmyr/plantemoji/uv", msg);

  pump_status.toCharArray(msg,pump_status.length()+1);
  client.publish("student/CASA0014/plant/ucfnmyr/plantemoji/pumpStatus", msg);
  
  humidifier_status.toCharArray(msg,humidifier_status.length()+1);
  client.publish("student/CASA0014/plant/ucfnmyr/plantemoji/humidifierStatus", msg);

}
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

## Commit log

2022-10-29 Trying to port the LCD driver to Huzzah, after a lot of attemps, it works now! But got a problem of maximum execution time which I'm try to solve for now
    [DEV_Config.h]
2022-10-29 Solved: by adding a yeild function inside LCD driver; turned out Huzzah doesn't allow more than 1.5 seconds for any loop to be executed
2022-10-31 First real Serial connection from Arduino to Huzzah, now sending fake sensor data in real time
2022-10-31 Remove LCD code from Arduino because I decided to connect it to Huzzah instead
2022-10-31 Sorting up LCD driver code
2022-10-31 Read LDR value from Arduino and send it to Huzzah
2022-10-31 Read humidity & temperature values from Arduino and send them to Huzzah
2022-10-31 Trying to connect to WPA2 Enteprise (eduroam)... seems it won't work
    [Huzzah.ino]
2022-10-31 Revert all WPA2 changes
    [Huzzah.ino]
2022-10-31 For comparison reasons; adding the nails again to compair values with the capacitive sensor
2022-10-31 Remove LDR sensor values for now
2022-11-01 Correct my moisture MQTT topics (nails & capacitive)
    [Huzzah.ino]
2022-11-01 Sort up Arduino code & some refactoring
2022-11-02 Add my Grafana dashboard sample
2022-11-02 Add a schematic diagram
    [Schematic.sch]
2022-12-01 Connecting Soil Temperature sensor using Arduino (DS18B20)
2022-12-02 Success in getting soil temperature from the DS18B20 sensor and send it via serial
2022-12-05 Create new PCB for plantemoji and finish the first draft of the schematic
    [Plantemoji.brd, Plantemoji.sch]
2022-12-05 Putting all the components on the board without routing for now
    [Plantemoji.brd]
2022-12-06 Finish wiring the PCB
    [Plantemoji.brd]
2022-12-06 Final touches before gerber files export
    [Plantemoji.brd]
2022-12-06 PCB is sent to PCBWay! Gerber files were generated using this tutorial (https://www.pcbway.com/helpcenter/technical_support/Generate_Gerber_files_in_Eagle.html)
    [Plantemoji.brd, Plantemoji.sch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]
2022-12-09 Added BOM for the PCB
2022-12-10 Added the full water level sensor & pump holders
    [Water level sensor holder.stl, Water pump holder - bottom cover.stl, Water pump holder - main body.stl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]
2022-12-10 Added an Arduino serial echo code (used while connected to ATmega 8A)
2022-12-10 Added Fusion360 project file & re-order 3d design files
    [Water bucket v15.f3d, Water level sensor holder.stl, Water pump holder - bottom cover.stl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]
2022-12-10 Added a schematic picture for the PCB
2022-12-12 Finished all the 3D enclosures!
    [Plant pot devices v17.f3d, Screen-body-cover.stl, Screen-body.stl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]
2022-12-12 Add an exported version of Fusion360 project
    [Plant pot devices v17.f3d, Plant pot devices v34.f3d]
2023-01-20 Remove G-code files as they can be produced from the STL objects
2023-01-20 Remove redundant Arduino code
2023-01-20 Remove the old schematic
    [Schematic.sch]
2023-01-20 Replace schematic diagram
2023-02-15 Add the DHT22 library and read values from the sensor
2023-02-15 Fixed a bug: sprintf() wasn't able to format double numbers, this was fixed by enabling the built-in functionality from compiler settings (taken from: https://startingelectronics.org/articles/atmel-A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
2023-02-16 Failed to compile, codebase now is too big - trying to reduce size
    [i2c.c, main.c]
2023-02-19 Continue attempts to make the SI1145 sensor working, the problem is mainly in the I2C connection
    [main.c]
2023-02-19 Trying to re-implement I2C connection from scratch
2023-02-20 After several days of debugging, I solved the I2C communication bug with the SI1145. Turned out the AVR TWI interface only includes basic byte exchange operations, without any software implementation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
    [SI1145_WE.c, SI1145_WE.h, i2c.c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]
2023-02-20 Fixed a bug in the SI1145_WE library, the address is set after initialisation whether it should be before initialisation!
    [SI1145_WE.c, SI1145_WE.h, main.c]
2023-02-20 Re-add all the sensors and add the final one (HW-390) - soil humidity sensor
2023-02-20 Fix a conflict in serial output, caused somehow internally in the MCU
    [main.c]
2023-02-21 Finalise the Atmega8A code, now all sensor data are being sent to Huzzah via serial
2023-02-21 Re-order and rename sensor readings
2023-02-21 Finish implementing MQTT sensor values publishing on Huzzah
2023-02-21 Fix a bug in MQTT transmission; a missing digit was at the end of every sensor value
    [Huzzah.ino]
2023-02-23 Re-scale sensor values and describe all used units in the documentation section
2023-02-23 Correct the soil humidity scale, now it's percentage
    [main.c]
2023-02-27 Fix variable overflow bug
    [main.c]
2023-02-27 Fix the soil humidity percentage: it was based on the ADC reading and was measuring the anti-humidity actually. Now it's the same unit as the air humidity
    [main.c]
2023-03-01 Port the Waveshare LCD driver to ESP32
2023-03-01 Revert "Port the Waveshare LCD driver to ESP32"
    This reverts commit b5bb7dba6c93a93275532fa44551edcafff9af1f.
    [Huzzah.ino, LCD_DEV_Config.h]
2023-03-01 Move the new ported ESP32 codebase to a new folder
2023-03-05 Major update to the PCB: now it's based on ESP32 (FireBeetle) instead of the old ESP8266 (Feather Huzzah)
    [Plantemoji.brd, Plantemoji.sch]
2023-03-05 The new PCB is sent to PCBWay (using this procedure: https://www.pcbway.com/helpcenter/technical_support/Notes_for_Gerber_files_Generated_from_Eagle_9_20.html)
    [copper_bottom.gbr, copper_top.gbr, drill_1_16.xln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]
2023-03-05 Add the library used for ESP32 footprint in Eagle (taken from: componentsearchengine.com)
2023-03-09 Trying a demo to auto-control the pump and humidifier
2023-03-09 Fixed a bug: the pump controlling port caused a conflict with the serial output
    [main.c]
2023-03-13 Add more documentation for controlling the pump and the humidifier
2023-03-13 Added the pump & humidifier control feature (to be controlled by Huzzah) in addition to reporting these states over serial
2023-03-13 Add a missing documentation
    [main.c]
2023-03-13 Add the new values (pump and humidifier states)
2023-03-13 Subscribe to pump and humidifier control topic on MQTT
2023-03-13 Implemented pump and humidifier manual control via MQTT
2023-03-14 Code refactor: using general pin numbers
2023-03-14 Trying to make TinyML demo on ESP32, I used @djdunc 's code from https://github.com/ucl-casa-ce/casa0018/blob/main/Week4/arduino/hello_casa
2023-03-14 Made some adaptations to the TinyML code in order to work on ESP32
2023-03-19 Add the exported air temperature dataset
2023-03-19 Add the exported soil temperature dataset
2023-03-20 Add some analysis of temperature & humidity readings in CE lab so far
2023-03-20 Add my discussion with Will about the last humidity and temperature results
2023-03-21 Completing merging all sensor readings in the Python script, in preparation to find correlation between them - still facing a problem here
2023-03-21 Fixed an issue with data correlation calculation, turned out Python was importing my sensor values as objects not floats
2023-03-21 Added a merged dataset from 5-3-2023 to 8-3-2023
    [merged-dataset-from-5-3-2023-to-8-3-2023.csv]
2023-03-23 Folders refactoring
    [merged-dataset-from-5-3-2023-to-8-3-2023.csv]
2023-03-24 Change main device photo in Readme.md
